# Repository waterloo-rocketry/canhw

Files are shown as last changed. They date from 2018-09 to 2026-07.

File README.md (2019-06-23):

## RocketCAN Hardware

This repository tracks the hardware development for the RocketCAN project. All schematics, board designs, and fabrication files are tracked in this repository. The corresponding software running on each board can be found in the `cansw_*` repositories. The CAN driver library used is tracked in the `canlib` repository.

All hardware files were developed in KiCAD.

### System Architecture

The RocketCAN project is an extension of the 2018 Flight Instrumentation project. The functions of the original Flight Instrumentation electronics are decoupled into several single-function modules connected by a Controller Area Network (CAN bus). The 2019 RocketCAN configuration consists of a radio board, an injector valve driver, a vent valve driver, a flight sensor suite, a system logger, and a GPS receiver. The modules freely share information over the CAN bus, allowing all modules to access resources such as the radio transceiver and sensor module. This minimizes the amount of component and functionality duplication, as well as power consumption (especially by the radio module). Power consumption is reduced further by allowing the radio board to control power to the rest of the system, forcing it into a low-power state while the rocket is idle. The resulting PCBs are also significantly smaller and easier to mount inside the rocket. Finally, RocketCAN’s configuration is easily extensible. A new subsystem simply needs to include a CAN communication module, after which it can communicate with all other boards on the bus. Potential extensions such as a flight computer, a state estimation module, or an air braking system would be able to use existing sensor data without implementing their own independent sensor suite.

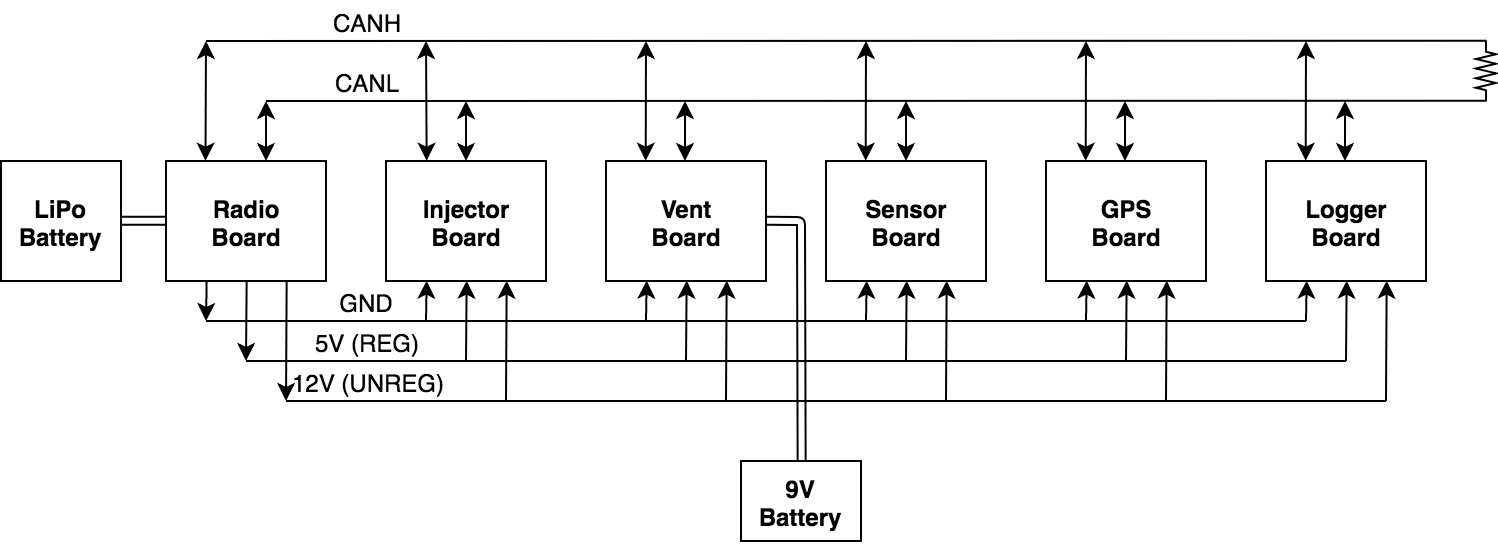
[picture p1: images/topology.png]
topo


At present, the radio board integrates with Waterloo Rocketry's Remote Launch Control System (RLCS), from which it receives instructions. It is also capable of broadcasting sensor data to RLCS.  The radio board communicates with the tower-side box of RLCS, which relays the data to the client-side box at mission control.

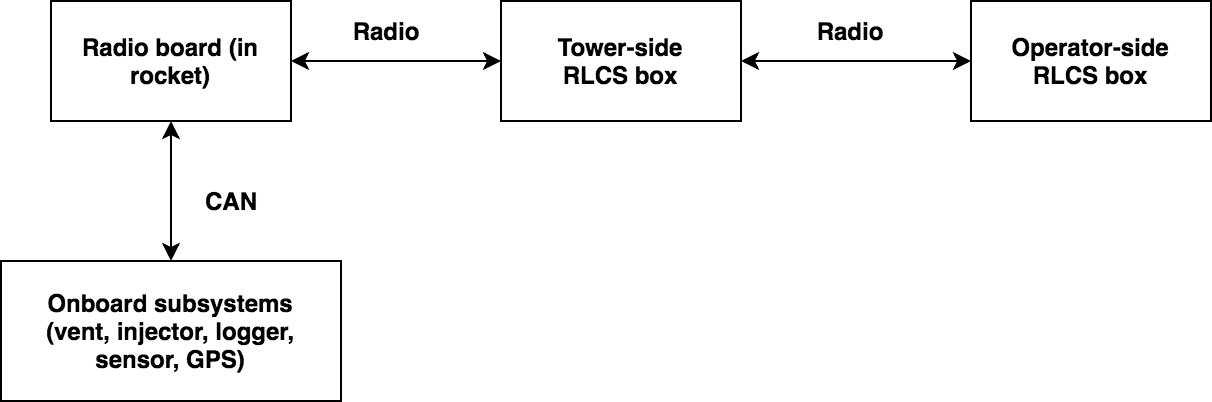
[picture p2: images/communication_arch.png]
comms


The CAN protocol was chosen for its high data rate, priority-based arbitration, and abundance of inexpensive hardware. The bus can safely be used by many boards at once without the risk of a low-priority message (eg. sensor data) preempting a high-priority message (eg. valve command). Microcontrollers with CAN modules, stand-alone CAN modules, and CAN transceivers are all widely available, making it cheap and simple to add CAN functionality to a subsystem.

Further descriptions and instructions for using each individual board are available in the README in the relevant board's directory.

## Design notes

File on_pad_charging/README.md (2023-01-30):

# On the Pad Charging
A charger board on the CAN bus that includes the battery, charging port connection, and additional power connections to live telemetry transmitter.
Clickup: https://app.clickup.com/8608989/v/li/176275976
Drive: https://drive.google.com/drive/folders/1WU_OsI1vf2b53sMAvz4AfjsN1jmYpsuN?usp=sharing

The system must provide CAN communication to the rocket from the ground side as long as the rocket is on the pad
The system should report the charge status, battery voltage, and current to CAN bus
The system should be able to turn off or on the CAN bus power. LTT should be kept 
The connector must be strong enough to stay in by itself, but weak enough to be pulled off by the rocket without affecting the launch

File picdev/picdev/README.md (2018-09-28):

This is a development board meant to be used for writing firmware for the CAN bus project while the main rocket boards are still in the hardware design phase. The board contains a PIC18F26K83 (which will be used on most subsystem boards inside the rocket) and a PIC16F1455 (which is used on the USB debug board). The PIC16F is connected to an external CAN module, allowing the two PICs to communicate with each other over CAN. 

The board is nicknamed "Keto" because it was borne out of a dislike of breadboards.

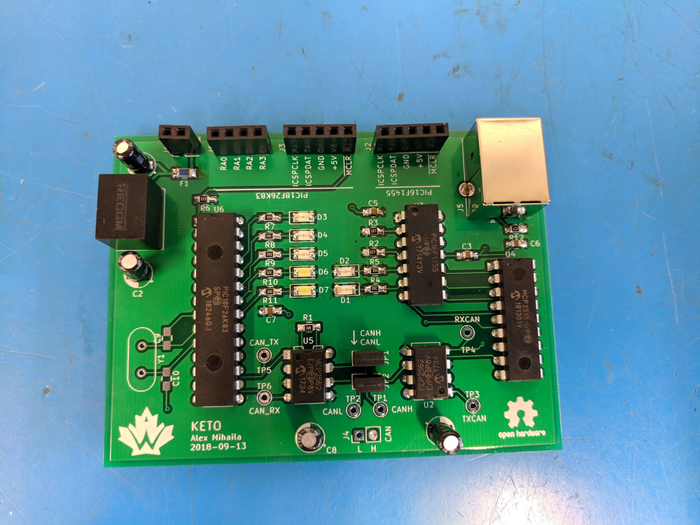
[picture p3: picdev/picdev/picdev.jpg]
picdev


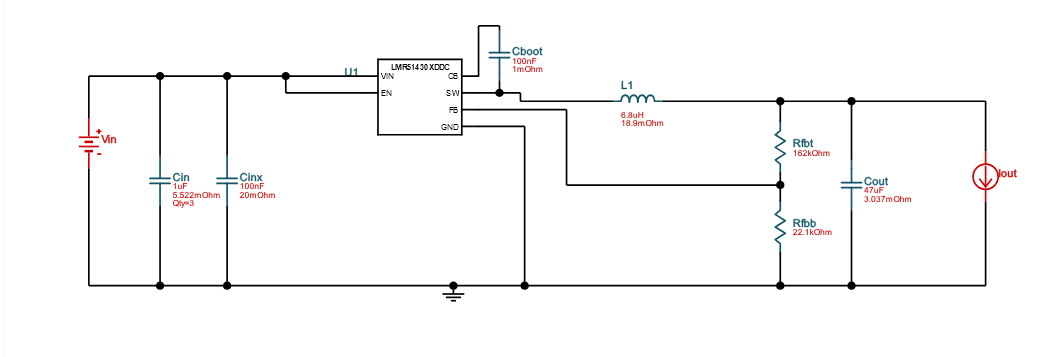
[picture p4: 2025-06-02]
rocket_power_board/WEBench Design.png

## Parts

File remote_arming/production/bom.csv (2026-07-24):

Designator | Footprint | Quantity | Value | LCSC Part #
BZ1 | Buzzer_12x9.5RM7.6 | 1 | CMI-1295-0585T
BZ2 | Buzzer_12x9.5RM7.6 | 1 | CMI-1295-1285T
C1, C2 | 0603 | 2 | 100nF
C10, C9 | 0603 | 2 | 26pF
C11 | 0603 | 1 | 0.39uF
C3 | 0603 | 1 | 10uF
C4 | 0603 | 1 | 0.1u
C5 | 0603 | 1 | 100n
C6 | 0603 | 1 | 0.33u
C7, C8 | 0603 | 2 | 0.1uF
D1, D2 | D_SOD-323_HandSoldering | 2 | CUS08F30
DB1, DR1, DW1 | 1206 | 3 | LED
F1 | 0603 | 1 | 0603L025YR
F2 | 1206 | 1 | Polyfuse 350mA
J1 | PinSocket_5x2.54_SMD_90deg_952-3198-1-ND | 1 | Conn_01x05_Female
J2 | BarrierBlock_ED2945-ND | 1 | Battery 1
J3 | connector_Harwin_G125-MH104M4-04AD000P | 1 | CAN connector
J4 | connector_Harwin_G125–MG10605M4P | 1 | Altimeter Input
J5 | JST_EH_S3B-EH_1x03_P2.50mm_Horizontal | 1 | SL Data Connector
J6 | connector_Harwin_G125–MG10605M4P | 1 | A1 Connections
JP1 | SolderJumper-2_P1.3mm_Open_RoundedPad1.0x1.5mm | 1 | M1 Pull Up
JP2 | SolderJumper-2_P1.3mm_Open_RoundedPad1.0x1.5mm | 1 | D1 Pull Up
Q1, Q2 | SOT-23_Handsoldering | 2 | BSS138
Q3 | SOT-23_Handsoldering | 1 | DMG2302UK
Q4 | TO-252-2 | 1 | AOD417
R1, R16, R18, R20, R21, R22, R5, R7, R9 | 0603 | 9 | 10K
R10 | 1206 | 1 | 4mR
R11 | 0603 | 1 | 200mR
R12 | 0603 | 1 | 2k
R13 | 0603 | 1 | 270R
R14 | 0603 | 1 | 5k
R15 | 0603 | 1 | 10kR
R17, R19, R6, R8 | 0603 | 4 | 27k
R2, R3, R4 | 0603 | 3 | 330R
TP1 | TestPoint_Pad_D2.0mm | 1 | SL_TX
TP2 | TestPoint_Pad_D2.0mm | 1 | CURR_CAN
TP3 | TestPoint_Pad_D2.0mm | 1 | CURR_BATT
U1 | SOIC-8_3.9x4.9mm_P1.27mm | 1 | MCP2562
U2 | SOIC-28W_7.5x18.7mm_P1.27mm | 1 | PIC18F26K83
U3 | Mag Switch | 1 | Mag Switch
U4 | SOT230P700X180-4N | 1 | UA78M05IDCYR
U5, U6 | SOT-23-5_HandSoldering | 2 | INA180
Y1 | Crystal_SMD_Abracon_ABM8G-4Pin_3.2x2.5mm | 1 | ABM8G-12.000MHZ-18-D2Y-T

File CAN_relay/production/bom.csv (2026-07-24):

Designator | Footprint | Quantity | Value | LCSC Part #
C1, C10, C11, C12, C13, C14, C16, C17, C18, C19, C21, C3, C8, C9 | 0603 | 14 | 100n
C2 | 0603 | 1 | 10n
C20, C23, C24 | 0805 | 3 | 22u
C22, C4 | 0603 | 2 | 1u
C5, C6 | 0603 | 2 | 2.2u
C7 | 0603 | 1 | 4.7u
D1 | 1206 | 1 | RED
D2 | 1206 | 1 | GREEN
D3, D4 | Nexperia_CFP3_SOD-123W | 2 | PMEG2010ER
D5, D6 | SOT-23 | 2 | ESDCAN01-2BLY | C1976606
F1 | 1206 | 1 | PTC 250mA
J2, J3 | connector_Harwin_G125-MH104M4-04AD000P | 2 | G125-MH104M4-04AD000P
R1, R2 | 0603 | 2 | 10k
R3, R4 | 0603 | 2 | 330R
R5, R6 | 0603 | 2 | 120R
U1 | LQFP-100_14x14mm_P0.5mm | 1 | STM32H750VBTx
U2, U3 | TCAN3413DDFR | 2 | TCAN3413DDFR
U4 | TPSM33606S3QRDNRQ1 | 1 | TPSM33606S3QRDNRQ1
X1 | Oscillator_SMD_Abracon_ASE-4Pin_3.2x2.5mm | 1 | ASE-4.000MHZ-L-C-T | C437121

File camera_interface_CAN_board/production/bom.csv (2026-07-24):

Designator | Footprint | Quantity | Value | LCSC Part #
C1, C2 | 0603 | 2 | 27pF
C10, C3, C4, C5, C9 | 0603 | 5 | 0.1uF
C11, C16, C6 | 0603 | 3 | 1uF
C12, C15 | 0603 | 2 | 2.2nF
C13, C14, C8 | 0805 | 3 | 10uF
C7 | 0603 | 1 | 10nF
D1 | 1206 | 1 | WHITE
D2 | 1206 | 1 | RED
D3 | 1206 | 1 | BLUE
D4 | D_SMF | 1 | SMF13CA
J1 | PinSocket_5x2.54_SMD_90deg_952-3198-1-ND | 1 | Programming Header
J2 | connector_Harwin_G125-MH104M4-04AD000P | 1 | G125-MH104M4-04AD000P
J3 | PinSocket_1x02_P1.27mm_Vertical | 1 | Analog_Video
J4 | connector_Harwin_G125–MG10605M4P | 1 | G125-MG10605M4P
R1, R2, R3, R8 | 0603 | 4 | 330R
R10 | 0603 | 1 | 120R
R11 | 0603 | 1 | 0R
R12, R14 | 0603 | 2 | 2k
R13 | 0603 | 1 | 1k
R4, R9 | 0603 | 2 | 10K
R5 | 0603 | 1 | 390k
R6 | 0603 | 1 | 3.3k
R7 | 0805 | 1 | 40mR
TP1 | TestPoint_Pad_D1.0mm | 1 | 5V
U1 | SOIC-28W_7.5x18.7mm_P1.27mm | 1 | canhw:PIC18F26K83
U2 | SOIC-8_3.9x4.9mm_P1.27mm | 1 | canhw:MCP2562
U3 | TPS25947xx | 1 | TPS259472ARPW
U4 | SOT-23-5_HandSoldering | 1 | INA180A3
U5 | SOP65P490X110-8N | 1 | TPS22958NDGKR
Y1 | Crystal_SMD_Abracon_ABM8G-4Pin_3.2x2.5mm | 1 | ABM8G-12.000MHZ-18-D2Y-T

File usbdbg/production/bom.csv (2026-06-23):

Designator | Footprint | Quantity | Value | LCSC Part #
C1, C2, C3 | 0603 | 3 | 0.1u
C15, C7 | 0603 | 2 | 10nF
C4 | 0603 | 1 | 10u
C6 | 0603 | 1 | 1uF
C8 | 0805 | 1 | 10uF
D1 | 1206 | 1 | GREEN
D2 | 1206 | 1 | RED
F1 | 1206 | 1 | 1A
J1 | PinSocket_5x2.54_SMD_90deg_952-3198-1-ND | 1 | Programming Header
J3 | CONN_SD-43045-001_04_MOL | 1 | BUS CONN
J4 | 2171790001_MOL | 1 | USB_C_Receptacle_USB2.0_14P
JP1, JP2 | PinHeader_1x02_P2.54mm_Vertical | 2 | Jumper
R1, R2 | 0603 | 2 | 330R
R3, R4 | 0603 | 2 | 10k
R5 | 0603 | 1 | 120R
R6, R7 | 0603 | 2 | 5.1k
R9 | 0603 | 1 | 6.65k
TP1, TP2, TP3, TP4 | KEYSTONE_5116 | 4 | TestPoint
U1 | SOIC-14_3.9x8.7mm_P1.27mm | 1 | PIC16F1455
U2 | SOIC-18W_7.5x11.6mm_P1.27mm | 1 | MCP2515
U3 | SOIC-8_3.9x4.9mm_P1.27mm | 1 | MCP2562
U4 | TPS25947xx | 1 | TPS259472ARPW
U5 | SOT-23-6 | 1 | USBLC6-2SC6

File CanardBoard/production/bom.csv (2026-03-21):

Designator | Footprint | Quantity | Value | LCSC Part #
C1, C10, C11, C14, C16, C18, C21, C22, C23, C24, C33, C34, C37, C40, C48, C50, C55, C57, C6, C60, C61, C62, C66, C67, C7, C73, C8, C81, C82, C83, C84, C9, C92, C93 | 0402 | 34 | 0.1uF | C85858
C12, C17, C47, C56, C63, C65, C74, C76, C89 | 0805 | 9 | 22uF | C86816
C13, C3, C5, C72, C91 | 0402 | 5 | 1uF | C77007
C15, C27, C28, C29, C30, C58, C59 | 0402 | 7 | 10nF | C91601
C19, C20, C25, C26, C51, C52, C53, C54, C70, C71, C85, C86, C87, C88 | 0603 | 14 | 0.1uF | C3011652
C2, C4, C49 | 0402 | 3 | 2.2uF | C77002
C31, C32, C90 | 0805 | 3 | 0.1uF | C882587
C35, C36, C38, C41, C43, C45, C68, C69, C79 | 1210 | 9 | 10uF | C77102
C39, C42, C44, C46 | A786MW227M1HLAV011 | 4 | 220uF | A786MW227M1HLAV011
C64 | 0402 | 1 | 220nF | C126524
C75 | 0402 | 1 | 33pF | C126506
C77, C78 | 1210 | 2 | 47uF | C77101
D1 | EAST1616RGBB2 | 1 | LED_RGBA | C6606484
D10, D17 | SOT-23 | 2 | ESDCAN01-2BLY | C1976606
D11, D12, D8, D9 | D_SMA | 4 | SMAJ28A | C148227
D13, D14, D15, D16, D4, D5, D6, D7 | D_SOD-523 | 8 | RB520S30T1G | C154821
D18, D19 | D_SMF | 2 | SMF15CA | C1851361
D2, D3 | D_SMA | 2 | SMAJ28CA | C148228
D20, D21, D22 | 0603 | 3 | RED | C2986060
F1, F2 | 1206 | 2 | 20A | C2838910
F3, F4, F5, F6 | 1206 | 4 | 10A | C41367232
F7, F8 | 1206 | 2 | 1.5A | C883133
F9 | 1206 | 1 | 5A | C41367229
FB1 | 0402 | 1 | BLM15AG121SN1D | C85812
J10 | connector_Harwin_G125-MH104M4-04AD000P | 1 | G125-MH104M4-04AD000P
J11 | Movella-1374028 | 1 | Movella-1374028
J12 | 1374027 | 1 | 1374027
J2 | microSD_HC_Molex_47219-2001 | 1 | Micro_SD_Card | C164170
J3, J4 | AMASS_XT30PW-M | 2 | XT30PW-M
J5 | G125MH10805M41AD1ADP | 1 | Motor 2
J6 | G125MH10805M41AD1ADP | 1 | Motor 1
J7 | G125MH10805M41AD1ADP | 1 | Motor 4
J8 | G125MH10805M41AD1ADP | 1 | Motor 3
J9 | USB_C_Receptacle_GCT_USB4105-xx-A_16P_TopMnt_Horizontal | 1 | USB_C_Receptacle_USB2.0_16P | C165948
L1 | SRP7050WA | 1 | 4.7uH | C19947706
Q1, Q2, Q3, Q4 | PowerPAK_SO-8_Single | 4 | SIR626DP-T1-RE3
Q10, Q7, Q8, Q9 | Infineon-PG-TSDSON-8 | 4 | 20N06D | C7543835
Q5, Q6 | 2N7002W | 2 | 2N7002W | C232391
R1, R14, R16, R2, R33, R34, R37, R38, R41, R42, R47, R48, R49, R8 | 0402 | 14 | 10k | C144807
R13, R15, R17, R19, R21, R23, R35, R36, R39, R40, R50, R52, R54, R55, R56, R59, R61, R67 | 0402 | 18 | 100k | C144809
R18, R20 | 0402 | 2 | 3.16k | C227034
R22, R24, R6, R7 | 0402 | 4 | 2.2k | C144773
R25, R26 | 0402 | 2 | 0R | C226739
R27, R28, R4, R5 | 0402 | 4 | 100R | C144808
R29, R30 | R_Shunt_Vishay_WSKW0612 | 2 | 1mR | C1517439
R3, R72, R73 | 0402 | 3 | 330R | C226996
R31, R32 | 0402 | 2 | 10R | C144805
R43, R44, R65 | 0805 | 3 | 120R | C727984
R45, R46 | 0402 | 2 | 5.1k | C144745
R51, R53, R68 | 0402 | 3 | 19.1k | C226835
R57 | 0402 | 1 | 34k | C227006
R58 | 0402 | 1 | 681R | C416567
R62 | 0402 | 1 | 43.2k | C278596
R63, R64, R69, R74, R75 | 0402 | 5 | 1k | C144789
R70, R71 | 0805 | 2 | 5m | C728267
R76 | 0805 | 1 | 1M | C228604
R9 | 1206 | 1 | 5.1k | C229719
U1 | LQFP-100_14x14mm_P0.5mm | 1 | STM32H733VGTx
U10, U11, U12, U9 | SOT-23-6 | 4 | LM74700
U13, U16, U6 | TCAN3413DDFR | 3 | TCAN3413DDFR
U14 | TPS25947xx | 1 | TPS259472 | C3662789
U15 | LGA-12_2x2mm_P0.5mm | 1 | LSM303AGR
U17 | LMR51460 | 1 | LMR51460 | C41802645
U18 | TPSM33606S3QRDNRQ1 | 1 | TPSM33610S3QRDNRQ1
U19, U20 | SOT-23-5 | 2 | INA180A3 | C122882
U2 | LGA-8_3x5mm_P1.25mm | 1 | MS5611-01BA
U21 | LSM6DSV32XTR | 1 | LSM6DSV32XTR
U22 | EMIF06MSD02N16 | 1 | EMIF06-MSD02N16 | C5267594
U23, U3 | WSON-6-1EP_2x2mm_P0.65mm_EP1x1.6mm | 2 | TVS3300DRV | C2863624
U4, U5 | LM749x0 | 2 | LM749x0
U7 | SOT-23-6 | 1 | USBLC6-2SC6 | C7519
U8 | MX25L25645GM2I-08G | 1 | MX25L25645GM2I-08G
X1 | Oscillator_SMD_Abracon_ASE-4Pin_3.2x2.5mm | 1 | ASE-4.000MHZ-L-C-T | C437121

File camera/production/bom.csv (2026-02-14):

Designator | Footprint | Quantity | Value | LCSC Part #
C1, C11, C12, C13, C14, C15, C16, C32, C33, C4, C7 | 0603 | 11 | 100n
C10 | 0603 | 1 | 4.7u
C17 | 0603 | 1 | 1u
C19, C20 | 0603 | 2 | 10p
C2 | 0603 | 1 | 22u
C21 | 0603 | 1 | 0.1u
C31 | 0603 | 1 | 10u
C49 | 0603 | 1 | 1uF | C49678
C5, C6 | 0603 | 2 | 33u
C50 | 0603 | 1 | 0.1uF | C49678
C8, C9 | 0603 | 2 | 2.2u
D1, D2, D5 | Nexperia_CFP3_SOD-123W | 3 | PMEG2010ER
D3 | 1206 | 1 | RED
D4 | 1206 | 1 | GREEN
F1 | 1206 | 1 | PTC 250mA
F2, F3 | 1206 | 2 | PTC 550mA
J2 | USB_Micro-B_Molex_47346-0001 | 1 | USB_B_Micro
J3 | PinHeader_2x07_P1.27mm_Vertical_SMD | 1 | Programmer
J5 | microSD_Molex_WM6698CT-ND | 1 | Micro_SD_Card
J6 | connector_Harwin_G125-MH104M4-04AD000P | 1 | G125-MH104M4-04AD000P
L1 | L_Bourns_SRP5030T | 1 | SRP5030T-3R3M
R1 | 0603 | 1 | 30mR
R10, R11, R12, R13, R14 | 0603 | 5 | 47k
R2 | 0603 | 1 | 40k
R3 | 0603 | 1 | 10k
R4 | 0603 | 1 | 33.2k 1%
R47, R48, R49 | 0603 | 3 | 10k | C17414
R5 | 0603 | 1 | 10k 1%
R8, R9 | 0603 | 2 | 100R
U1 | SOT-23-5_HandSoldering | 1 | INA180
U2 | SOT-23-6_Handsoldering | 1 | TPS562200
U4 | LQFP-100_14x14mm_P0.5mm | 1 | STM32H750VBTx
U5 | SOIC-8_3.9x4.9mm_P1.27mm | 1 | LTC2875-S8
U8 | SOIC-8_5.3x5.3mm_P1.27mm | 1 | MX25L25645GM2I-08G
Y1 | Crystal_SMD_Abracon_ABM8G-4Pin_3.2x2.5mm | 1 | ABM8G-32.000MHZ-B4Y-T

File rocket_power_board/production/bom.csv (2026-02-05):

Designator | Footprint | Quantity | Value | LCSC Part #
12IL, 5IL | TestPoint_Pad_1.0x1.0mm | 2 | TestPoint
C1, C13, C14, C15 | 0603 | 4 | 10uF
C10, C11, C23 | 0603 | 3 | 0.1u
C12, C19, C20, C22 | 0805 | 4 | 22uF
C16 | 0603 | 1 | 100nF
C17, C6 | 0603 | 2 | 2.2n
C18 | 0603 | 1 | 100p
C2 | 0603 | 1 | 0.1uF
C21, C8, C9 | 0603 | 3 | 1.0uF
C3, C4 | 0603 | 2 | 27pF
C5 | 0603 | 1 | 1uF
C7 | 0603 | 1 | 100pF
D1 | 1206 | 1 | RED
D2 | 1206 | 1 | BLUE
D3 | 1206 | 1 | WHITE
D4 | D_SOD-128 | 1 | PMEG3030EP
D5 | D_SOD-123F | 1 | SMF4L13CA
D6 | D_SOD-123F | 1 | SS24FL
D7 | D_SOD-123F | 1 | P4SMF5.0CA
D8 | D_SOD-123F | 1 | PMEG1020EH,115
F1 | 0154Series_LTF | 1 | 0154005.DRL
J1 | PinSocket_5x2.54_SMD_90deg_952-3198-1-ND | 1 | Programming Connector
J2 | connector_Harwin_G125-MH104M4-04AD000P | 1 | G125-MH104M4-04AD000P
J3 | TE_2-1437667-4 | 1 | 4DB-P108-02
L1 | IND_VLS6045EX-3R3N | 1 | 3.3uH
R1 | 0603 | 1 | 120R (DNP)
R10 | 0603 | 1 | 10mR
R11 | 0603 | 1 | 470k
R12 | 0603 | 1 | 14.7k
R13, R23, R25 | 0603 | 3 | 50k
R14, R29 | 0603 | 2 | 20k
R15, R28 | 0603 | 2 | 1.67k
R16, R19, R27, R30, R33, R4, R6 | 0603 | 7 | 10k
R17, R31 | 0603 | 2 | 71.5k
R18 | 0603 | 1 | 83.5k
R2 | 0603 | 1 | 220k
R20, R21, R34 | 0603 | 3 | 1.5k
R22 | 0603 | 1 | 400k
R24 | 0603 | 1 | 180k
R26 | 0603 | 1 | 56.2k
R3 | 0603 | 1 | 100k
R32 | 0603 | 1 | 30.5k
R5 | 0603 | 1 | 15k
R7 | 0603 | 1 | 500R
R8, R9 | 0603 | 2 | 330R
U1 | SOIC-8_3.9x4.9mm_P1.27mm | 1 | MCP2562
U2 | SOIC-28W_7.5x18.7mm_P1.27mm | 1 | PIC18F26K83-I/SO
U3, U7 | Texas_RPW0010A_VQFN-10_2x2mm | 2 | TPS259474ARPWR
U4 | SOT-23-5 | 1 | INA180A3
U5, U8 | SOT-23-5 | 2 | OPA333AIDR
U6 | SOT-23-6 | 1 | TPS563200
Y1 | Crystal_SMD_Abracon_ABM8G-4Pin_3.2x2.5mm | 1 | ABM8G-12.000MHZ-18-D2Y-T

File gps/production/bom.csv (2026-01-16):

Designator | Footprint | Quantity | Value | LCSC Part #
C1, C10, C13, C7, C9 | 0603 | 5 | 22pF
C11, C12 | 0805 | 2 | 26pF
C14, C2, C6 | 0603 | 3 | 0.1uF
C3 | 0603 | 1 | 10uF
C4, C5 | 0603 | 2 | 1uF
C8 | 0603 | 1 | 2.2uF
D1 | 1206 | 1 | WHITE
D2 | 1206 | 1 | RED
D3 | 1206 | 1 | BLUE
D4 | D_SOD-123F | 1 | KDZVTR3.6B
F1 | 0603 | 1 | 0ZCM0008FF2G
J1 | PinSocket_5x2.54_SMD_90deg_952-3198-1-ND | 1 | Programming Header
J2 | connector_Harwin_G125-MH104M4-04AD000P | 1 | G125-MH104M4-04AD000P
J3 | TAOGLAS_EMPCB.SMAFSTJ.B.HT | 1 | EMPCB.SMAFSTJ.B.HT
L1, L2 | 0603 | 2 | 47nH
R1 | 0603 | 1 | 100R
R2, R3, R4 | 0603 | 3 | 10k
R7, R8 | 0603 | 2 | 160
R9 | 0603 | 1 | 200mR
TP1 | TestPoint_THTPad_1.0x1.0mm_Drill0.5mm | 1 | RX
TP2 | TestPoint_THTPad_1.0x1.0mm_Drill0.5mm | 1 | TX
TP3, TP4 | TestPoint_Keystone_5000-5004_Miniature | 2 | 36-5001-ND
U1 | QFN16_M10578_ANT | 1 | M10578-A2
U2 | SOIC-28W_7.5x18.7mm_P1.27mm | 1 | PIC18F26K83
U3 | SOIC-8_3.9x4.9mm_P1.27mm | 1 | MCP2562
U4 | SOT-23-5_HandSoldering | 1 | SPX3819M5-L-3-3
U5 | SOT-23-5_HandSoldering | 1 | INA180
Y1 | Crystal_SMD_Abracon_ABM8G-4Pin_3.2x2.5mm | 1 | ABM8G-12.000MHZ-18-D2Y-T

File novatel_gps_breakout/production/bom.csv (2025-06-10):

Designator | Footprint | Quantity | Value | LCSC Part #
C1, C2 | 0805 | 2 | 10u
F1 | 1206 | 1 | 350m
J1 | PTF11001LD | 1 | PTF-110-01-L-D
J2 | connector_Harwin_G125–MG10605M4P | 1 | Harwin Gecko
J3 | AMPHENOL_GMSB0522132EU | 1 | GMSB0522132EU
U1 | SOT-23-5_HandSoldering | 1 | TLV75533PDBV

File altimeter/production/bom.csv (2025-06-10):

Designator | Footprint | Quantity | Value | LCSC Part #
BZ1 | CUI_CMI-9605-1280T | 1 | CMI-9605-1280T
C1, C27, C28, C5 | 0805 | 4 | 10uF
C10, C11, C12, C17, C18, C20, C29, C7, C8 | 0805 | 9 | 100nF
C13, C9 | 0805 | 2 | 2.2uF
C14, C48 | 0805 | 2 | 4.7uF
C15, C16, C3, C30, C31, C49 | 0805 | 6 | 1uF
C19, C2, C35, C38, C42, C50 | 0805 | 6 | 0.1uF
C21, C22, C23, C24, C36, C37, C39, C40, C41, C43 | 0805 | 10 | 47nF
C25 | 0805 | 1 | 0.33uF
C26 | 0805 | 1 | 0.22uF
C32, C33, C34 | 0805 | 3 | 22uF
D2 | 1206 | 1 | YELLOW
D3 | 1206 | 1 | RED
D4 | 1206 | 1 | GREEN
D5 | Nexperia_CFP3_SOD-123W | 1 | PMEG2010ER,115
F1 | 2920 | 1 | 2920L700/24SLER
FB1 | 0805 | 1 | BLM21PG221SN1D
J1 | connector_Harwin_G125–MG10605M4P | 1 | GPS
J2 | connector_Harwin_G125–MG10605M4P | 1 | RocketCAN
J3 | connector_Harwin_M80-5000642 | 1 | M80-5000642
J4 | TE_2-1437667-4 | 1 | 4DB-P108-02
J5 | PololuAltIMUv6 | 1 | Pololu
J6 | PinSocket_2x02_P1.27mm_Vertical_SMD | 1 | Programmer
J7 | microSD_Molex_WM6698CT-ND | 1 | Micro_SD_Card
L1 | IND_IHLP-2525CZ_VIS | 1 | IHLP2525CZER2R2M11
R1 | 0805 | 1 | 0.05R
R10, R25, R32, R38, R39, R46, R52, R7, R8, R9 | 0805 | 10 | 5k
R11, R13, R29, R43 | 0805 | 4 | 60k
R12, R14, R28, R31, R35, R42, R45, R49 | 0805 | 8 | 20k
R15 | 0805 | 1 | 0.002R
R16, R75 | 0805 | 2 | 0.015R
R17, R18, R19, R20, R3, R4, R76, R77 | 0805 | 8 | 10R
R21 | 0805 | 1 | 33.2k
R22, R23, R24, R26, R37, R40, R51 | 0805 | 7 | 10k
R27, R36, R41, R50 | 0805 | 4 | 175R
R30, R44 | RES_PWR263S_BRN | 2 | PWR263S-35-5R00F
R33, R47 | 0805 | 2 | 1.5k
R34, R48 | 0805 | 2 | 500R
R67, R68, R69, R70, R71 | 0805 | 5 | 10kR
R72, R73, R74 | 0805 | 3 | 100R
U1 | SOIC-8_3.9x4.9mm_P1.27mm | 1 | MCP2562
U10, U12, U13, U9 | TLP3543A__6P4X7P12_TOS | 4 | TLP3543A(TP1,F)
U11, U14 | SOT-363_SC-70-6_Handsoldering | 2 | INA210AIDCKT
U18 | SOT-23-5_HandSoldering | 1 | INA180A3
U2 | SOT-23-5 | 1 | INA180A3
U4 | LQFP-100_14x14mm_P0.5mm | 1 | STM32H750VBTx
U5 | Mag Switch | 1 | Mag Switch
U6 | SOT-223 | 1 | NCV33275ST5.0T3G
U7 | SOT-23-6 | 1 | TPS563200DDCR
U8 | VSSOP-8_3x3mm_P0.65mm | 1 | INA2180A4IDGKR

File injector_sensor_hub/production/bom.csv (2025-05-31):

Designator | Footprint | Quantity | Value | LCSC Part #
2A1, 2A2, 2A3, 2A4, 2A5, 3A1, 3A2, 3A3 | TestPoint_Keystone_5005-5009_Compact | 8 | TestPoint
C1 | 0805 | 1 | 10uF
C2, C3 | 0805 | 2 | 0.1uF
C4 | 0805 | 1 | 0.1 uF
C5, C6 | 0805 | 2 | 27pF
D1 | 1206 | 1 | BLUE
D2 | 1206 | 1 | WHITE
D3 | 1206 | 1 | RED
F1, F2 | 1206 | 2 | 350mA
H1, H2 | MountingHole_3.2mm_M3_Pad | 2 | +5V
H3, H4 | MountingHole_3.2mm_M3_Pad | 2 | MountingHole_Pad
J1 | connector_Harwin_G125–MG10605M4P | 1 | CAN_Connector
J10, J3, J4, J6, J8 | JST_PH_S2B-PH-K_1x02_P2.00mm_Horizontal | 5 | Conn_01x02_Female-Connector
J2 | PinSocket_5x2.54_SMD_90deg_952-3198-1-ND | 1 | Programming Header
J5, J7, J9 | JST_PH_S3B-PH-K_1x03_P2.00mm_Horizontal | 3 | Conn_01x03_Female
R1, R10, R11, R12, R13, R14, R15, R16, R17, R18, R19, R2, R20, R21, R22, R9 | 0805 | 16 | TBD
R3 | 0805 | 1 | 10K
R4 | 0805 | 1 | 180R
R5 | 0805 | 1 | 220R
R6, R7 | 1206 | 2 | 130mR
R8 | 0805 | 1 | 300R
TP1 | TestPoint_Keystone_5005-5009_Compact | 1 | TP_5V
TP4 | TestPoint_Keystone_5005-5009_Compact | 1 | TP_12V
U1 | SOIC-8_3.9x4.9mm_P1.27mm | 1 | MCP2562
U2 | SOIC-28W_7.5x17.9mm_P1.27mm | 1 | PIC18F26K83
U3, U4 | SOT-23-5_HandSoldering | 2 | INA180
Y1 | Crystal_HC49-4H_Vertical | 1 | Crystal

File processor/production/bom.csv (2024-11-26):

Designator | Footprint | Quantity | Value | LCSC Part #
C1 | 0805 | 1 | 10uF | C15850
C10, C22, C3 | 0805 | 3 | 4.7uF | C1779
C11, C13, C15, C2, C20, C21, C5, C6, C7, C8, C9 | 0805 | 11 | 0.1uF | C49678
C12, C14, C16 | 0805 | 3 | 1uF | C28323
C17 | 0805 | 1 | 0.01uF | C1710
C18, C19 | 0805 | 2 | 2.2uF | C377773
C4 | 0805 | 1 | 22uF | C45783
D1 | 1206 | 1 | LED_R | C7496845
D2 | 1206 | 1 | LED_G | C7496843
D3 | 1206 | 1 | LED_B | C434440
D4 | 1206 | 1 | PWR | C434434
F1 | 1206 | 1 | Polyfuse 1A | C20800
FB1 | 0603 | 1 | PE-0603PFB121ST | C139186
JP3 | SolderJumper-3_P1.3mm_Open_Pad1.0x1.5mm_NumberLabels | 1 | BOOT_CTL
L1 | IND_DFE252012PD-1R0M=P2_MUR | 1 | 1uH | C2917900
R1 | 1206 | 1 | 33 mR | C912764
R10, R11, R12, R13, R14, R15, R16, R17, R18, R19, R20, R21, R7, R9 | 0805 | 14 | 10kΩ | C17414
R2 | 0805 | 1 | 453kΩ | C101739
R3 | 0805 | 1 | 100kΩ | C149504
R4, R8 | 0805 | 2 | 150Ω | C17471
R5, R6 | 0805 | 2 | 330Ω | C17630
U1 | SOIC-8_3.9x4.9mm_P1.27mm | 1 | MCP2562 | C191417
U2 | SOT-23-5_HandSoldering | 1 | INA180 | C2059240
U3 | DRL0006A | 1 | TLV62568ADRLR | C398372
U4 | LQFP-100_14x14mm_P0.5mm | 1 | STM32H733VGTx | C730160
U5 | LGA-14L_2p5X3p0X0p86_STM | 1 | LSM6DSV32X | C22461202
X1 | Oscillator_SMD_Abracon_ASE-4Pin_3.2x2.5mm | 1 | ASE-4.000MHZ-L-C-T | C437121

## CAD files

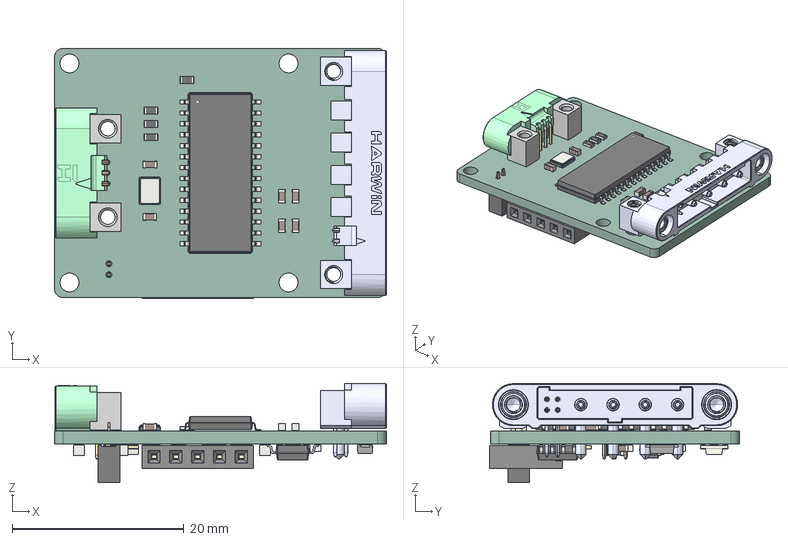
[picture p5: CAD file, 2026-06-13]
camera_interface_CAN_board/output/camera_board.step
38.7 x 29.1 x 11.6 mm
G125-3270696
G125-1060005_BENT x 3
G125-1070005_BENT x 3
R_0603_1608Metric x 8
C_0603_1608Metric x 13
SOIC-28W_7.5x18.7mm_P1.27mm
Crystal_SMD_Abracon_ABM8G-4Pin_3.2x2.5mm
g125-mh104m4-04ad000p
LED_1206_3216Metric x 3
C_0805_2012Metric x 3
SOIC-8_3.9x4.9mm_P1.27mm
D_SMF
M20-7910542R
MOLD
BODY_MUA08A
LEAD_MUA08A x 8
PinSocket_1x02_P1.27mm_Vertical
R_0805_2012Metric
SOT-23-5
camera_interface_CAN_board_PCB

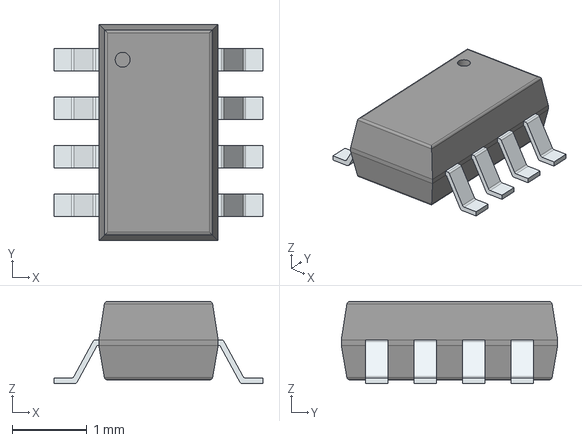
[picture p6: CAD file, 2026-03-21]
CAN_relay/3D_Models/TCAN3413DDFR.stp
2.80 x 2.90 x 1.10 mm
PinsArrayLR

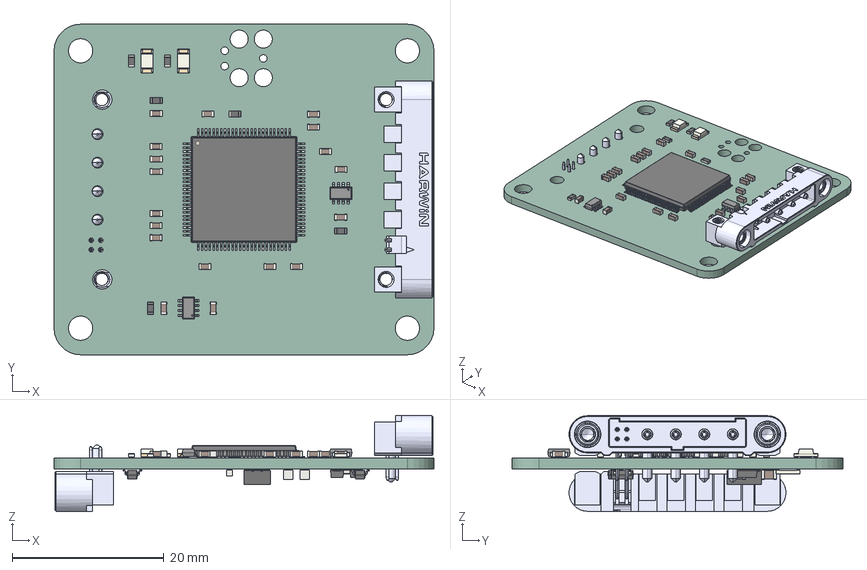
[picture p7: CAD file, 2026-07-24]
CAN_relay/CAN_relay.step
50.0 x 43.5 x 12.6 mm
g125-mh104m4-04ad000p x 2
C_0603_1608Metric x 20
R_0603_1608Metric x 6
PinsArrayLR x 2
LED_1206_3216Metric x 2
LQFP-100_14x14mm_P0.5mm
SOT-23 x 2
MOLD_CPOMPOUND_AF0
SOLID1-489_AF0
SOLID1-490_AF0
SOLID1-491_AF0
SOLID1-492_AF0
SOLID1-493_AF0
SOLID1-494_AF0
SOLID1-495_AF0
SOLID1-496_AF0
SOLID1-497_AF0
SOLID1-498_AF0
C_0805_2012Metric x 3
6081697a-9268-11ed-8af4-a0cec80452fd_part x 2
60816e3e-9268-11ed-8af4-a0cec80452fd_part x 2
6081710e-9268-11ed-8af4-a0cec80452fd_part x 2
6081737a-9268-11ed-8af4-a0cec80452fd_part x 2
Fuse_1206_3216Metric
CAN_relay_PCB

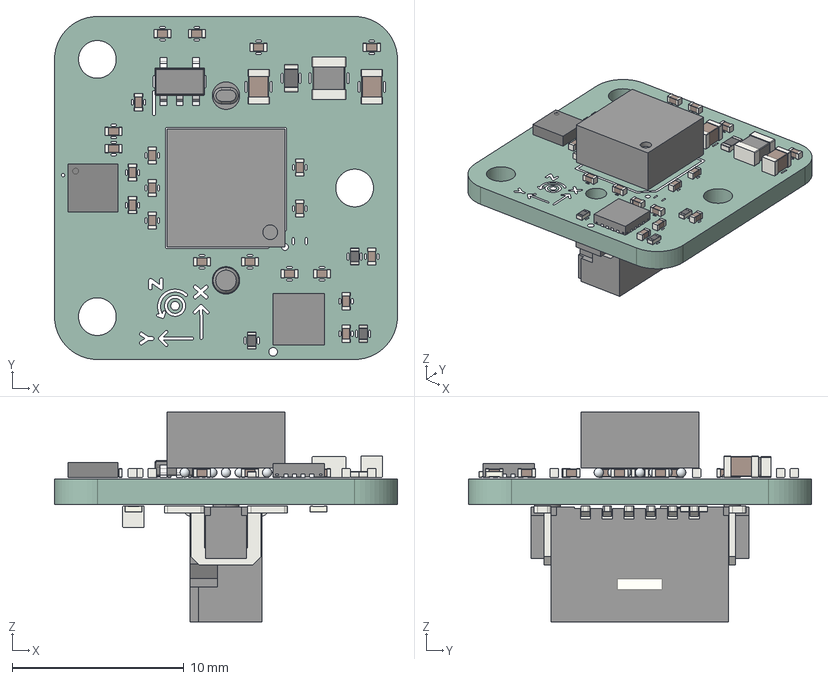
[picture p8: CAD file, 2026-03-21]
CanardBoard/AD_Breakout_Board/Output/AD_Breakout_REVA.step
20.0 x 20.0 x 12.2 mm
C_0402_1005Metric x 21
R_0402_1005Metric x 7
L_1008_2520Metric
ADXL380-1BCCZ-RL7
C_0805_2012Metric x 3
A2
A3
A4
A5
A6
B1
B3
B4
B5
B7
C1
C2
C6
C7
D1
D2
D6
D7
E1
E2
E6
E7
F1
F3
F4
F5
F7
G2
G3
G4
G5
G6
BODY-SOT
LEAD-SOT x 5
R_0603_1608Metric
LP_FR_1_27_MV_1_75_CONTACT.3 x 12
GEH_FR_1_27_12_MV_1_75_HOUSING
LR_FR_1_27_BOARD_LOCK.1 x 2
AD_Breakout_silkscreen x 2
AD_Breakout_PCB

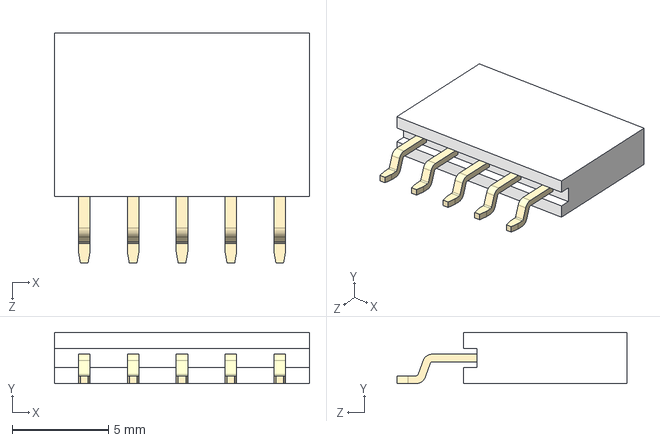
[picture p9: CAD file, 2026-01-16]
gps/Symbol_Footprt/BG300_05_A_L_A/BG300-05-X-X-A_REVC.step
13.2 x 2.65 x 12.0 mm
body^BG301-xxx
pin^BG301-xxx x 5

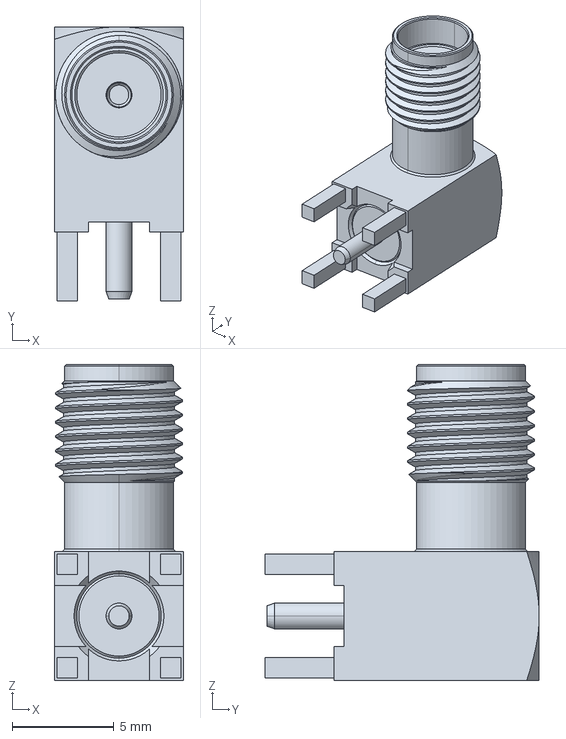
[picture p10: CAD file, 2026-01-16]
gps/Symbol_Footprt/SMA_Conn/c-3-1478978-1-f-3d.stp
6.35 x 13.5 x 15.6 mm

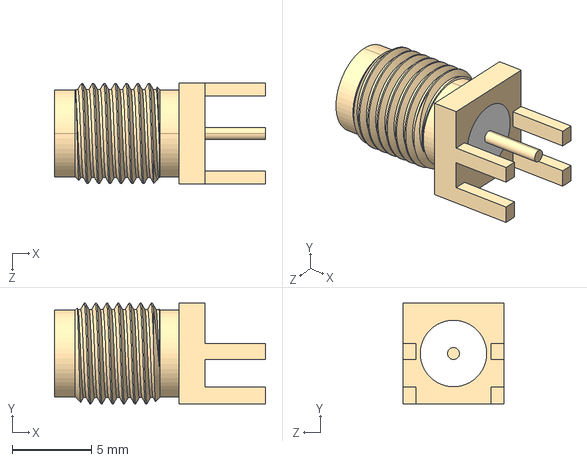
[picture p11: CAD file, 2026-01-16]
gps/Symbol_Footprt/SMA_Edge/CON-SMA-EDGE-S.step
13.3 x 6.35 x 6.35 mm

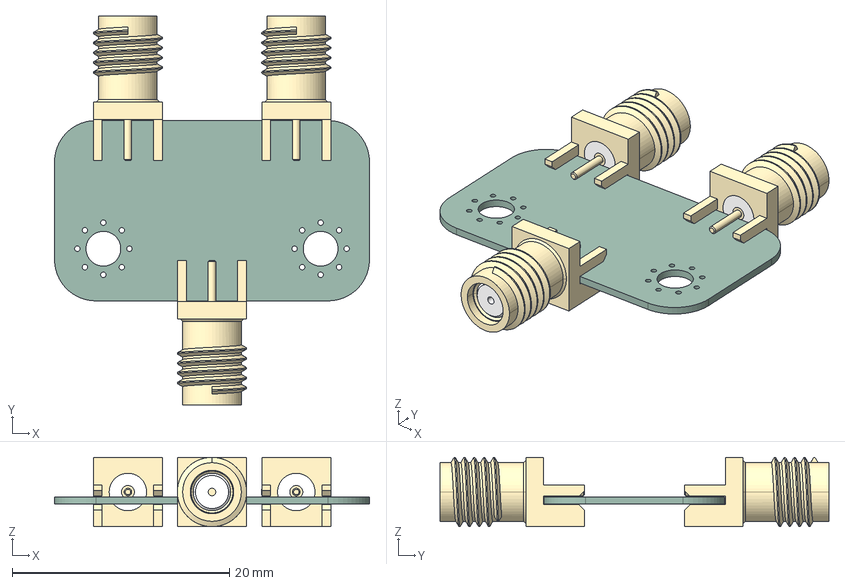
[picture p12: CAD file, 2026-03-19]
live_telemetry/power-splitter/power-splitter.step
29.0 x 35.8 x 6.38 mm
EMPCB.SMAFSTJ.B.HT x 3
power-splitter_PCB

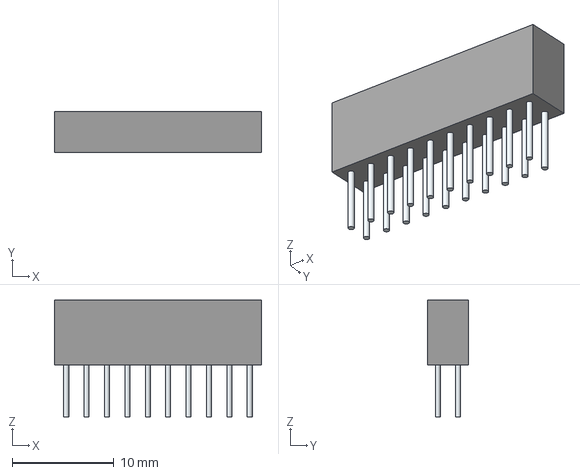
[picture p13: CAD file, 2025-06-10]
novatel_gps_breakout/3d/PTF-110-01-L-D.stp
20.3 x 4.00 x 11.4 mm
Leads x 20

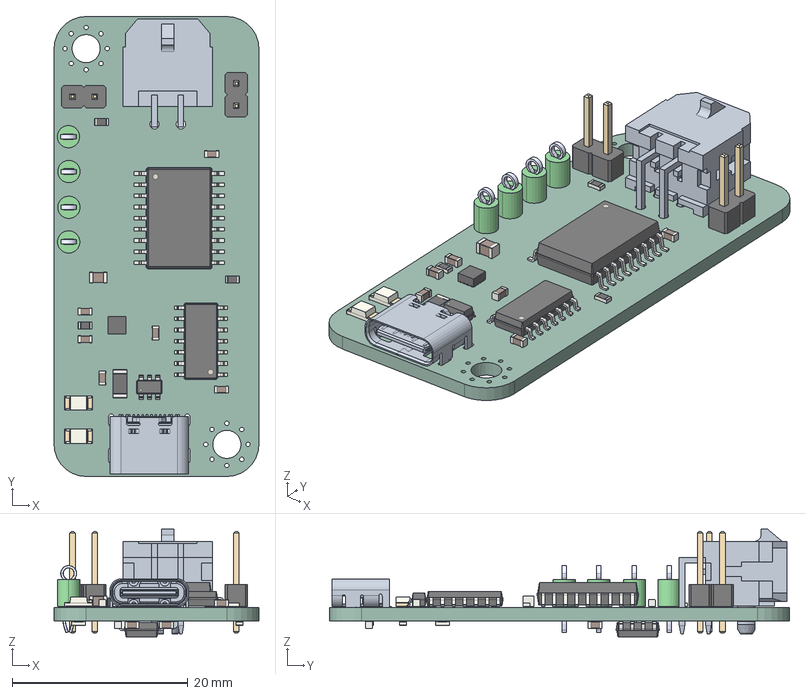
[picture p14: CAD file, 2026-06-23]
usbdbg/usbdbg.step
23.3 x 52.3 x 12.3 mm
C_0603_1608Metric x 9
PinHeader_1x02_P254mm_Vertical x 2
R_0603_1608Metric x 6
SOIC-18W_7.5x11.6mm_P1.27mm
SOIC-14_3.9x8.7mm_P1.27mm
C_0805_2012Metric
LED_1206_3216Metric x 2
SOT-23-6
MOLD
Fuse_1206_3216Metric
SOIC-8_3.9x4.9mm_P1.27mm
usbdbg_PCB

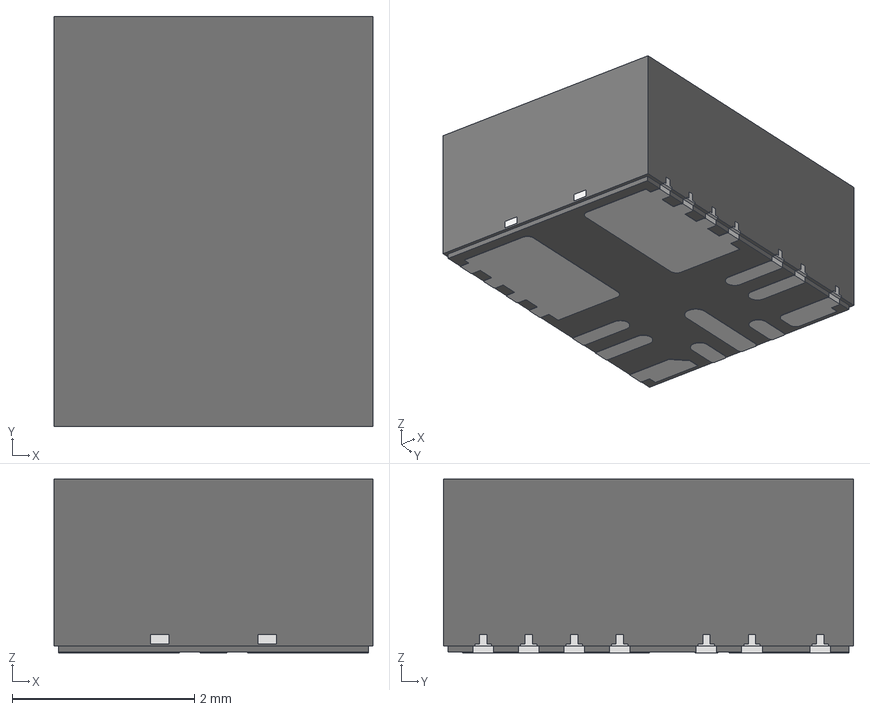
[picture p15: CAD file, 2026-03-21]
CAN_relay/3D_Models/RDN0011B.stp
3.50 x 4.50 x 1.91 mm
MOLD_CPOMPOUND_AF0
SOLID1-489_AF0
SOLID1-490_AF0
SOLID1-491_AF0
SOLID1-492_AF0
SOLID1-493_AF0
SOLID1-494_AF0
SOLID1-495_AF0
SOLID1-496_AF0
SOLID1-497_AF0
SOLID1-498_AF0

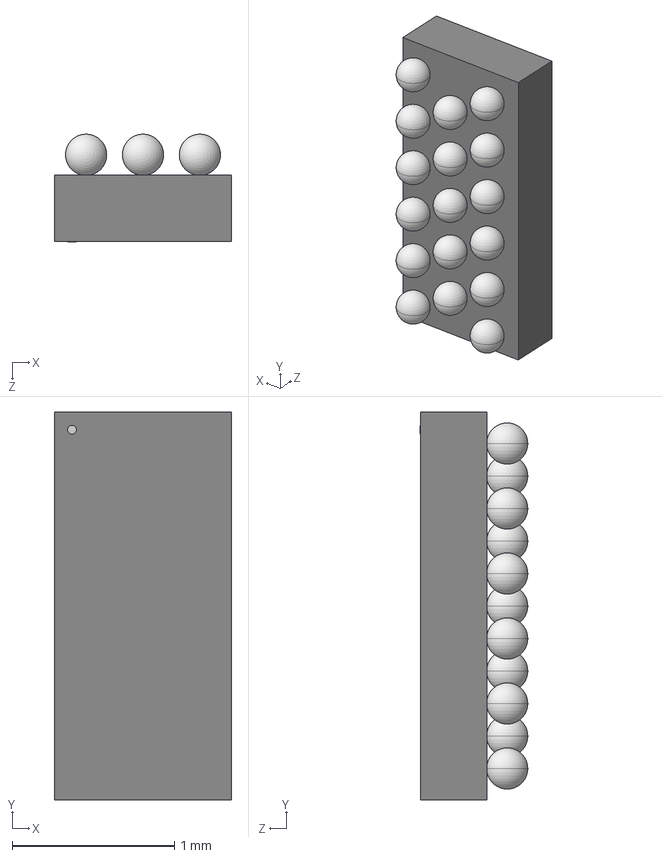
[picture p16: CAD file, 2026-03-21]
CanardBoard/3D_Models/EMIF06-HSD03F3.stp
1.09 x 2.39 x 0.663 mm

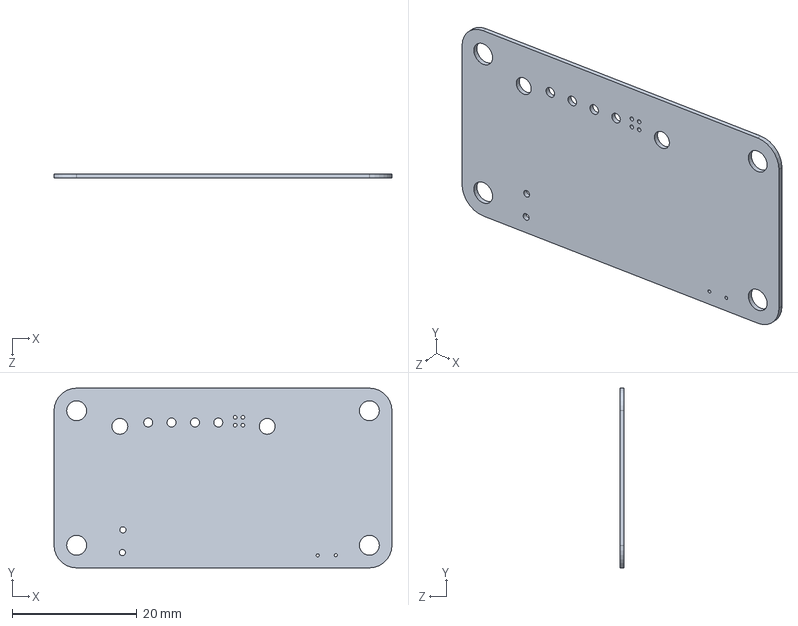
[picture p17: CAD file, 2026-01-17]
gps/gps_2_PCB.step.SLDPRT
54.3 x 28.9 x 0.665 mm

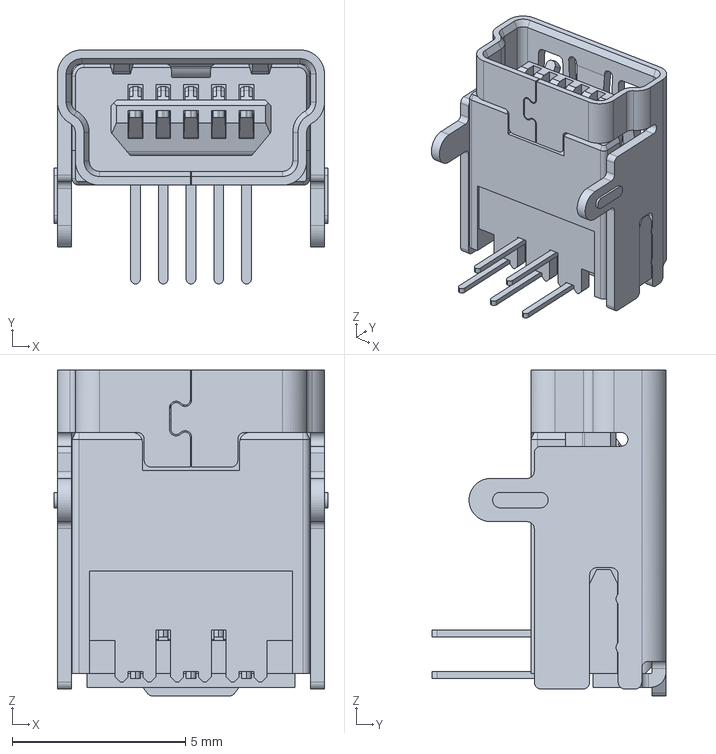
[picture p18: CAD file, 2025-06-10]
novatel_gps_breakout/3d/GMSB0522132EU.step
7.90 x 6.75 x 9.40 mm

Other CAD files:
gps/gps_2.step.SLDASM
CanardBoard/3D_Models/SIR626DP-T1-RE3.STEP
gps/SOIC-28W_7.5x18.7mm_P1.27mm.step.SLDPRT
CanardBoard/3D_Models/REF2041AIDDCR.stp
CanardBoard/3D_Models/1373827.stp
CanardBoard/3D_Models/2N7002W.stp
CanardBoard/3D_Models/472192001.stp
CanardBoard/3D_Models/A786MW227M1HLAV011.stp
CanardBoard/3D_Models/ADS1219IRTER.stp
CanardBoard/3D_Models/ADXL380-1BCCZ-RL7.stp
CanardBoard/3D_Models/ADXRS649BBGZ.stp
CanardBoard/3D_Models/BSZ024N04LS6ATMA1.stp
CanardBoard/3D_Models/EAST1616RGBB2.stp
CanardBoard/3D_Models/EMIF06-MSD02N16.stp
CanardBoard/3D_Models/G125-MH10805M4-1AD1ADP.stp
CanardBoard/3D_Models/LGA-14L_2p5X3p0X0p86_STM.step
CanardBoard/3D_Models/LM74910QRGERQ1.stp
CanardBoard/3D_Models/LMR51450FNDRRR.stp
CanardBoard/3D_Models/MX25L25645GM2I-08G-TR.stp
CanardBoard/3D_Models/PTVS30VZ1UPAZ.stp
CanardBoard/3D_Models/SRP7050WA.stp
CanardBoard/3D_Models/TPS25210LRPWR.stp
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

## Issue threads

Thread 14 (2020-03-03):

Boards list 26pF for oscillator filter caps, but these are not readily available.

zx100x100, 2020-03-03:
We already use 27pF as a substitution, we should fix the schematics to address this.

amihaila, 2020-03-03:
fixed in `537802ed4601e1b5135b2eaccdbe543847dbf9fd`

Closed 2020-03-03.

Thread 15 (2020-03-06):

Add Battery number to silkscreen on Remote Arming

zx100x100, 2020-03-06:

zx100x100, 2020-03-12:
add battery numbers to silk screen
fix can connector pinout to mach other boards
 put diodes and voltage sensing down stream of mag switches for easier power-up confirmation

zx100x100, 2020-03-21:
OUT and IN pins are backwards for mag switches

zx100x100, 2020-05-24:
Switch to 90 degree JST for altitude connector to avoid pinching wires with airframe

zx100x100, 2020-09-25:
label jumpers

zx100x100, 2020-11-18:
all this was dealt with in V2

Closed 2020-11-18.

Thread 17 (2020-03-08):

Not all schematic PDFs are up to date.

zx100x100, 2020-03-08:

amihaila, 2020-03-08:
fixed in `ac6cfa6a2df630c2c32a38dd9e6480b5804a335e`

Closed 2020-03-08.

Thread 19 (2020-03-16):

resistor value of R4 and R3 on logger should be 160, not 330

zx100x100, 2020-03-16:

zx100x100, 2020-03-16:
Package of U3 is wrong

zx100x100, 2020-03-16:
or part number - used MIC5504-3.3YM5-TR

Closed 2022-01-16.

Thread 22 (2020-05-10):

RF footprint needs to be improved

JaredWatson, 2020-05-10:
Currently the RF footprint used on the GPS board and the Live Telemetry board had extremely small pads that make soldering it a pain in the butt. In the future the amount of soldering space should probably be expanded (but not enough to shrink the space of the RF trace, it's already smaller than 120 mils and we don't want to lose that sweet sweet RF integrity).

QuantumManiac, 2020-05-11:
I did a bit of testing, and it seems like it's pretty simple to have different sized pads on different layers.

In the _Pad Properties_ window, there's a Copper setting which allows you to change the layers that the copper and other layers are on for the pad:
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

My solution is to overlap two pads at each through-hole, with one pad having F.Cu and F.Mask and the other B.Cu and B.Mask

Here's a view of a modified SMA connector in the footprint editor modified using the above method:
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
Notice that while the front pads are 2.2 mm, the back ones are much larger, at 3 mm

3D Views - front and back comparison:
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

If I got some measurements for what the pads should be on each side, I would be happy to modify the footprint.

JaredWatson, 2020-05-12:
Looks good, I'll leave a more formal review on the actual PR. This is definitely the footprint people should be using for SMA stuff in the future.

Closed 2020-05-21.

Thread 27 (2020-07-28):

Issues with first version of Live Telemery boards

dwkletke, 2020-07-28:
Issues marked with LTT are for the Live Telemetry Transmitter and issues marked with LTR are for the Live Telemetry Receiver.

dwkletke, 2020-07-28:
LTT: R12 and R13 silk screen labels need to be moved to become completely visible.

dwkletke, 2020-07-28:
LTT: Add values for R10, R11, and R_sense to schematic.

dwkletke, 2020-07-28:
LTT: Fix C5 and C9 labelling for +/- (right now is backwards).

dwkletke, 2020-07-28:
LTT: Add labeling for +/- on battery screw terminal.

dwkletke, 2020-07-28:
LTR: Add mounting hole(s).

dwkletke, 2020-07-28:
LTT and LTR: Add arrowhead to silk screen for MCLR pin on programming header.

Closed 2023-07-09.

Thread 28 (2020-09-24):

Vent board V2 Issues

zx100x100, 2020-09-24:
MCLR silkscreen reads 3.3V, but MCLR is actually a 5V line on this board

zx100x100, 2020-12-24:
A jumper was never added to allow vent to draw from the CAN bus. in addition, I'm not sure why we ever Ok'd a JST for flight critical connections

zx100x100, 2021-05-16:
Forgot to close this when we merged the V2.1 PR

Closed 2021-05-16.

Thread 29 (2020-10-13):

GPS board led label

Rio6, 2020-10-13:
The led connected to fix signal is labeled as "white", better label it as "fix" so it's more clear.

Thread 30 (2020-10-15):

Mini sensor issues

zx100x100, 2020-10-15:
1. The PTC fuse values should be labelled

2. this board could really do with some SMD test points.

zx100x100, 2020-12-17:
MCLR silkscreen does not indicate MCLR voltage

rdakhil, 2023-04-05:
some ground test points would be nice to have in the next respin

also standoffs are there in the CAD but they are very thin. the plating should be changed to be about as thick as the mounting holes

JasonBrave, 2023-05-23:
Clock source(oscillator) is not isolated, result interference from CAN, cause PIC think external oscillator failure.

BluCodeGH, 2023-07-09:
Recent comments are not addressed.

Joe-Joe-Joe-Joe, 2023-07-09:
Has this board not been respun since this issue was raised?

Closed 2023-07-09.

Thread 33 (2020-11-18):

Remote Arming Issues

zx100x100, 2020-11-18:
Arming currently has a 1.7V dropout regulator, that is way to high
replace with https://www.digikey.com/en/products/detail/texas-instruments/LM2931AMX-5-0-NOPB/334920

zx100x100, 2021-05-14:
Make the mag switch mounting holes make sense

Closed 2023-07-09.

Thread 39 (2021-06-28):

Logger CAN connector pinout is wrong

BluCodeGH, 2021-06-28:

Closed 2022-01-16.

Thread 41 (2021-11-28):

PICam CAN connector pinout is wrong

BluCodeGH, 2021-11-28:

Closed 2023-07-09.

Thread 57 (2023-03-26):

Charging Board Issues

BluCodeGH, 2023-03-26:
- There is no current sensing on VCC out of the powerpath switcher, which means that when we are powering the rocket off of the battery we have no idea what the current draw on the 12V line from the CAN bus is.
- There is significant interference between the 24->13V regulator (likely the inductor?) and its current sensing voltage. The current sense voltage at idle is about 12 mV and we're seeing 500 mV spikes on the pin highly regularly at 8.2 kHz.

Closed 2023-06-03.

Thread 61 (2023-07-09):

Minisensor rev. 2 issues

Joe-Joe-Joe-Joe, 2023-07-09:
New respin problems:

              missing solder standoffs,
              doesn't match the required design from Rocket CAD, make the two agree

_Originally posted by @zx100x100 in https://github.com/waterloo-rocketry/canhw/issues/30#issuecomment-1494538198_

              some ground test points would be nice to have in the next respin

              also standoffs are there in the CAD but they are very thin. the plating should be changed to be about as thick as the mounting holes

_Originally posted by @rdakhil in https://github.com/waterloo-rocketry/canhw/issues/30#issuecomment-1496845932_

              Clock source(oscillator) is not isolated, result interference from CAN, cause PIC think external oscillator failure.

_Originally posted by @JasonBrave in https://github.com/waterloo-rocketry/canhw/issues/30#issuecomment-1558394349_

Joe-Joe-Joe-Joe, 2024-03-28:
Closed by retiring minisensor lol

Closed 2024-03-28.

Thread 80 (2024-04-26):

Charging Board Re-respin todo

AshTheEngiqueer, 2024-04-26:
C27 can be an 0805 to match C26 and C28
R17 and R23 can be an 0805 to match R39
The layout could be nicer (like fix some of the scuffed traces, and have components align better in general)

AshTheEngiqueer, 2024-06-22:
13V current sense is scuffed, voltage sense is gigafucked - smth to do with inductor? unclear.

Lucifersan, 2024-06-29:
indicate that the motor control harwin should be horizontal and all that jazz

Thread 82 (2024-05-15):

Propulsion board issues

JasonBrave, 2024-05-15:
MCLR silkscreen is at wrong side of programming header lmao

miles-milne, 2024-07-05:
R18, R20, R22, and R28 should be rated as "TBD" rather than 90mR

BluCodeGH, 2024-07-06:
CAN connector pinout is wrong. Also the pinout of the motor control gecko is unintuitive and should be improved.

BluCodeGH, 2024-07-08:
LEDs on the back are hard to see

miles-milne, 2024-07-09:
Wrong fuse footprints used. Should be an appropriate size for PTC fuses

miles-milne, 2024-07-09:
General board issues, including daisy chaining, via-in-pad, somewhat sus traces, and board is too large (too many components on the front side)

Closed 2025-05-31.

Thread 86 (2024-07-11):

Camera board issues

BluCodeGH, 2024-07-11:
VREF capacitor missing, and should just connect to VDDA anyways?

BluCodeGH, 2024-07-26:
Tie 12->2.8v buck en pin to 5v / vusb so that turning off bus 5v turns off cameras

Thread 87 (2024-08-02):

Remote Arming Issues

BluCodeGH, 2024-08-02:
- Silkscreens got removed from all the datamate connectors
- Buzzers interfere with mag switches, they need to be moved further away

BluCodeGH, 2024-08-02:
- PIC-controlled buzzer causes interference with the batt2 current measurement when on

Tessa-P, 2024-08-03:
Batt current sense should be called altimeter current sense (and numbered respectively)

StarlightDescender, 2025-08-11:
already fixed in new PR for 2026 but
- swap to geckos for consistency with new boards

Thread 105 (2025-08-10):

RPB issues

StarlightDescender, 2025-08-10:
Efuses tripping intermittently
Board is larger than it needs to be

StarlightDescender, 2025-08-10:
no ground planes on front/back of pcb

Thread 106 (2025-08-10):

novatel breakout issues

StarlightDescender, 2025-08-10:
20 pin connector footprint doesnt match part

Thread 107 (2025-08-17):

logger board issues

StarlightDescender, 2025-08-17:
- no way to tell how full SD card is without removing it

SAT-oO, 2025-08-17:
is it feasible to `f_size` then add?

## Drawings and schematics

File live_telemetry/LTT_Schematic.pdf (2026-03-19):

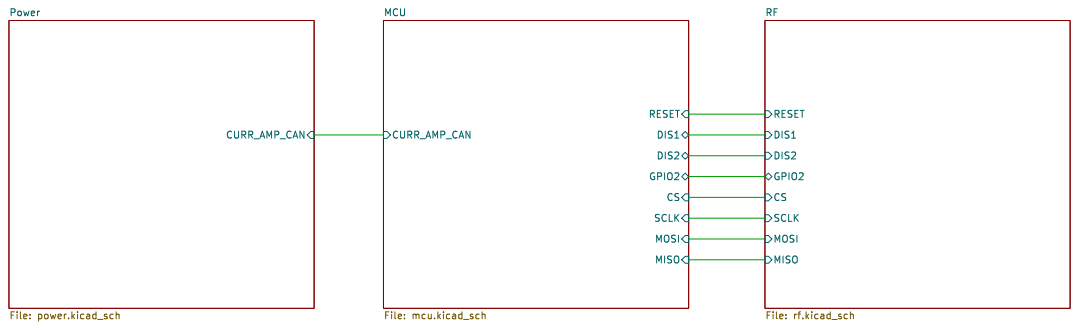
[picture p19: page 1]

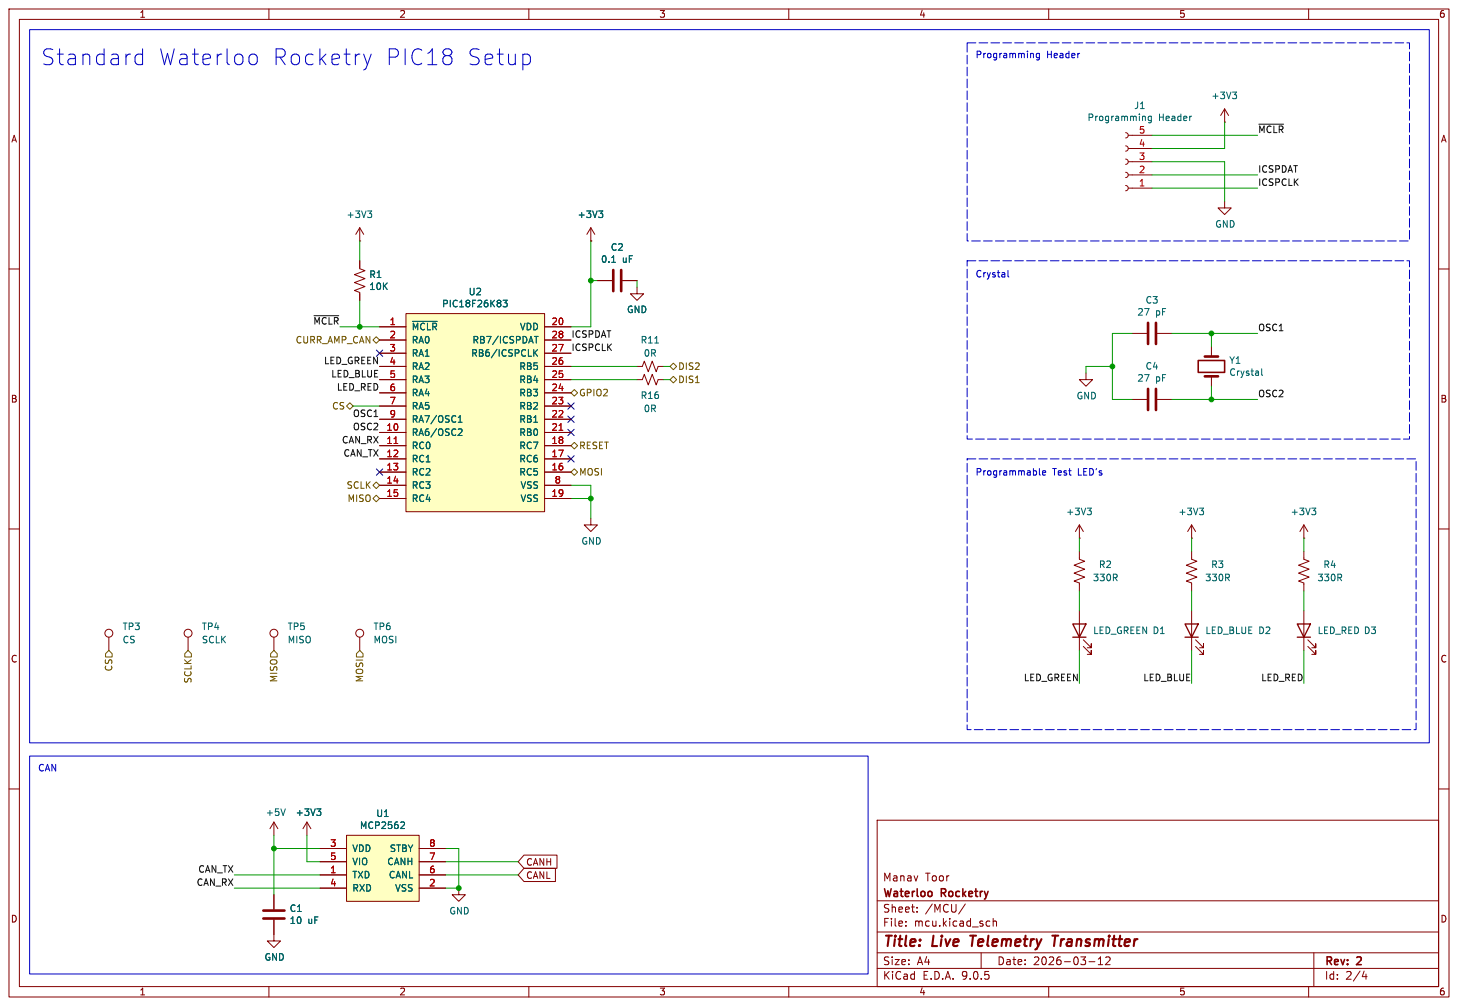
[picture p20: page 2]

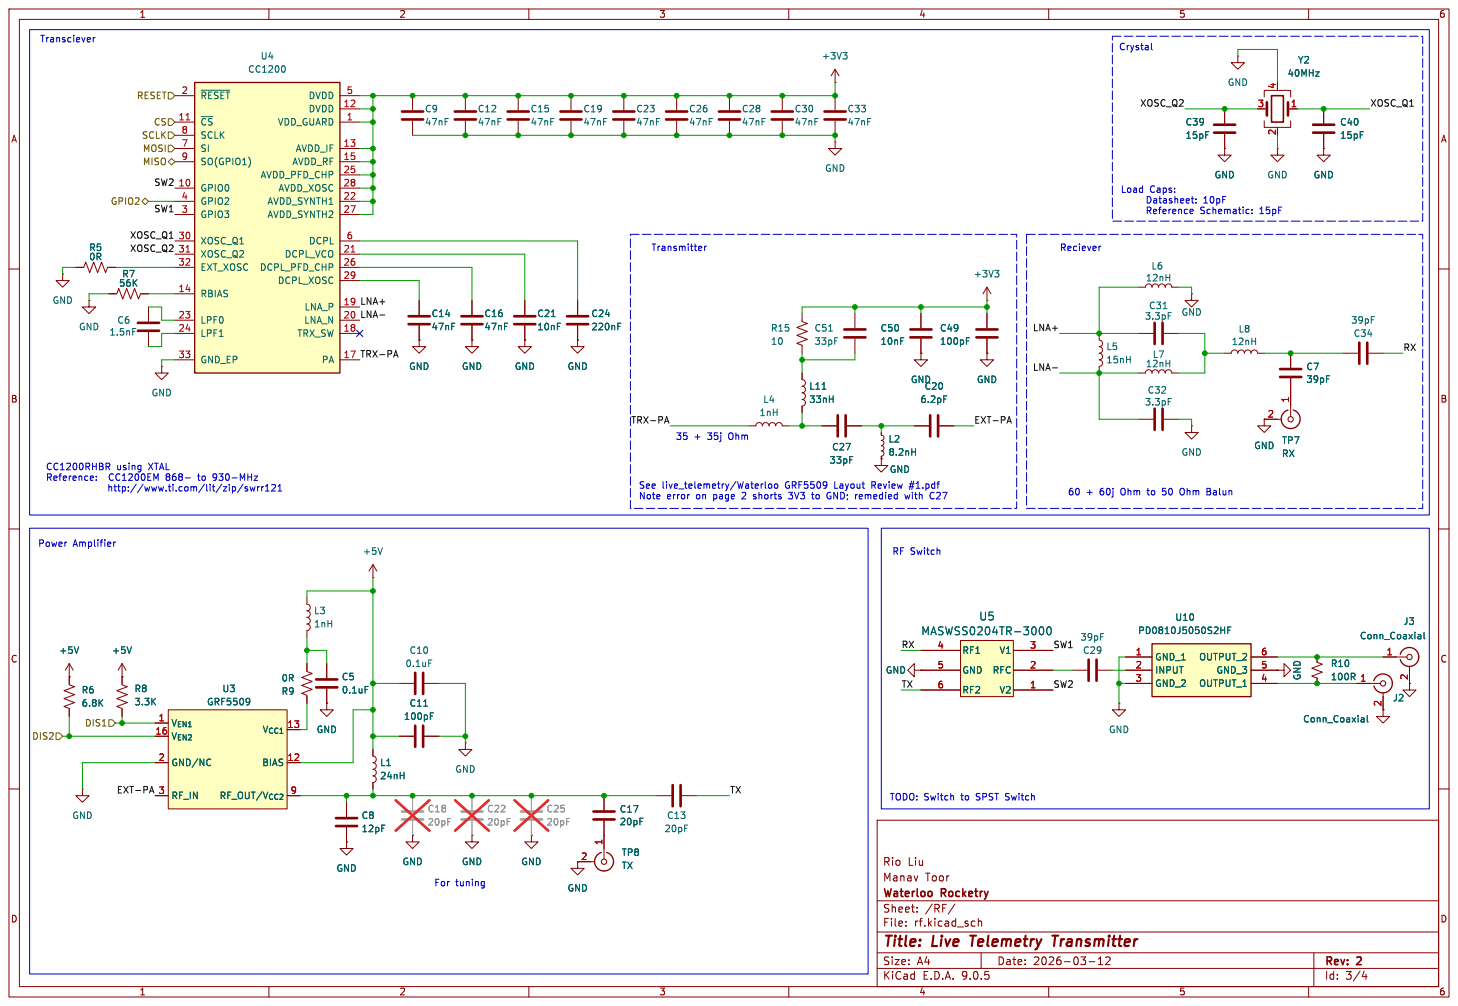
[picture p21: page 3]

2 R10 GND 100R U5 MASWSS0204TR-3000 RF1 4 GND 5 RF2 6 V1 3 RFC 2 V2 1 GND

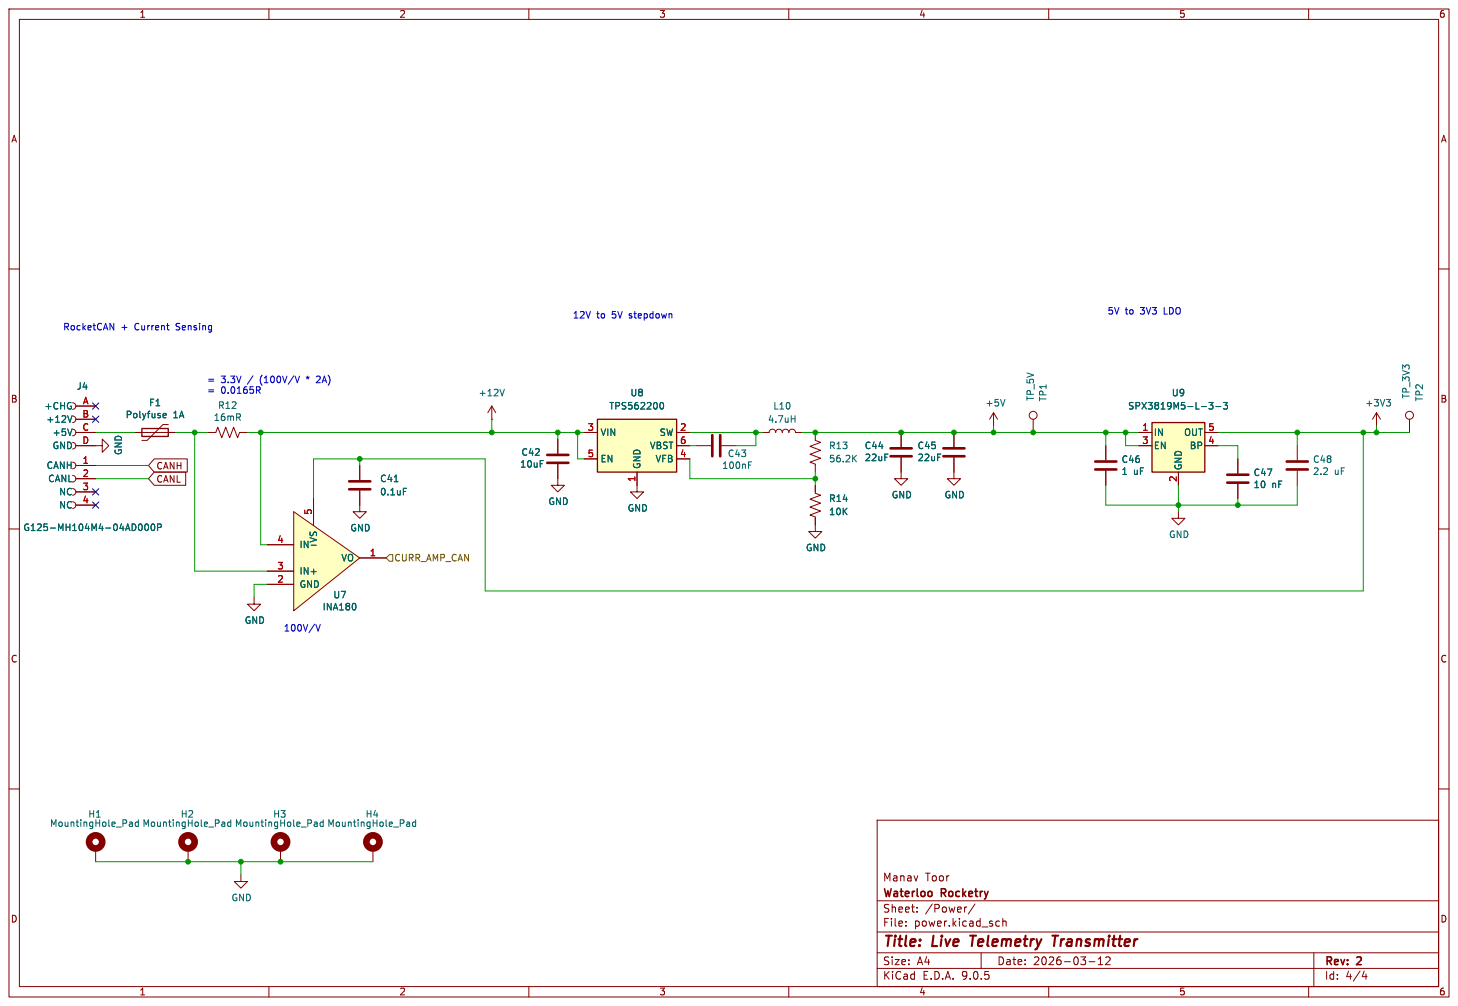
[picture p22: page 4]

1 SW 2 VBST 6 VFB 4 U8 TPS562200 GND GND GND

1 SW 2 VBST 6 VFB 4 GND

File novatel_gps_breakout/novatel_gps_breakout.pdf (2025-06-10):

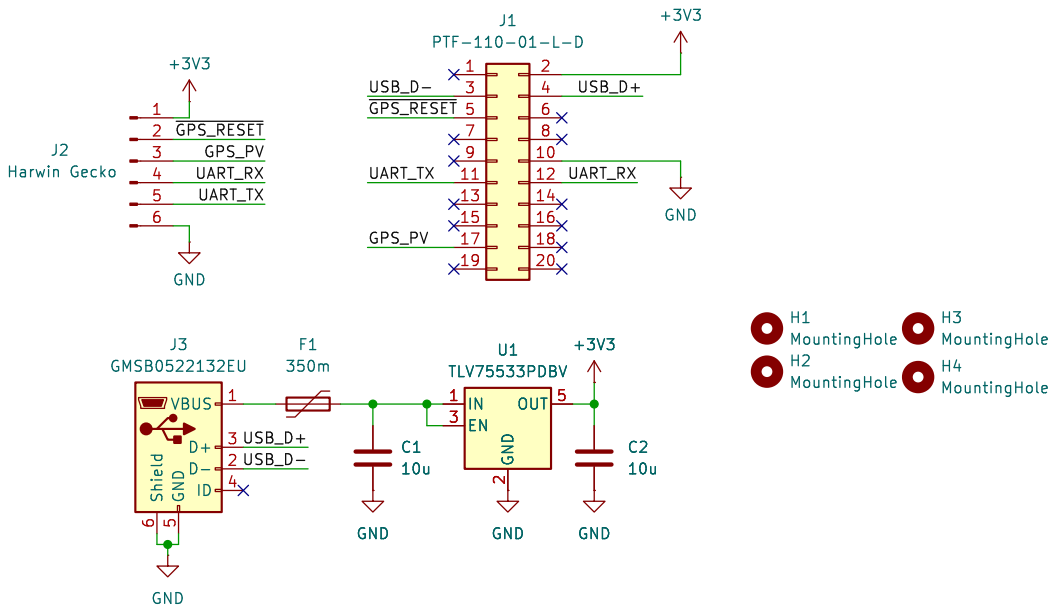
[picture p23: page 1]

Id: 1/1 Title: Novatel GNSS Reciever Breakout Board

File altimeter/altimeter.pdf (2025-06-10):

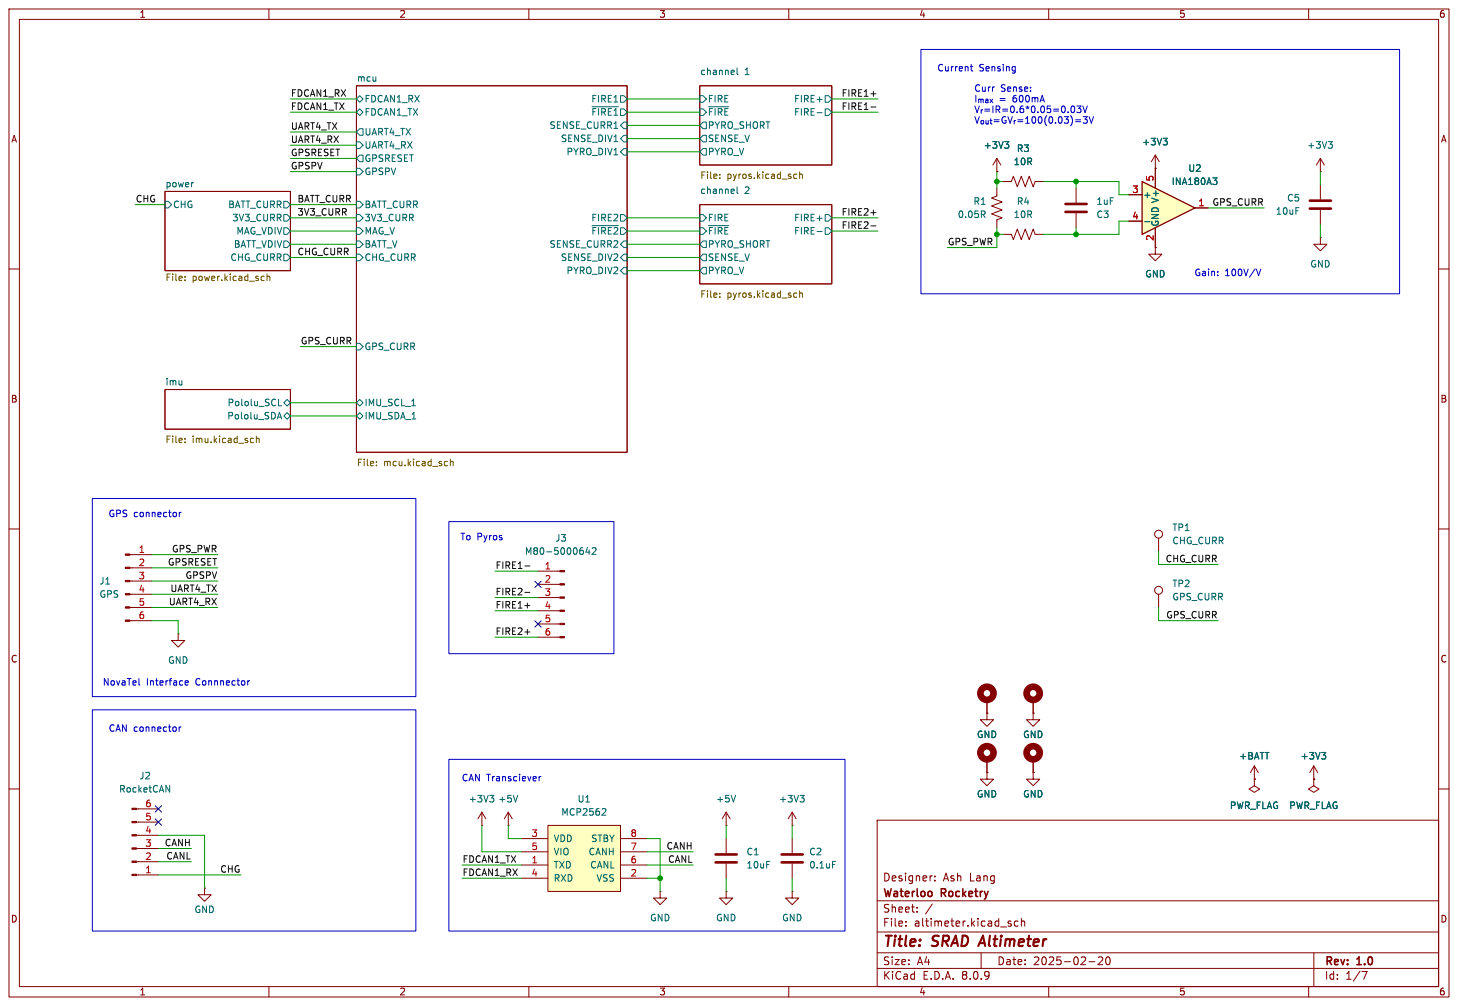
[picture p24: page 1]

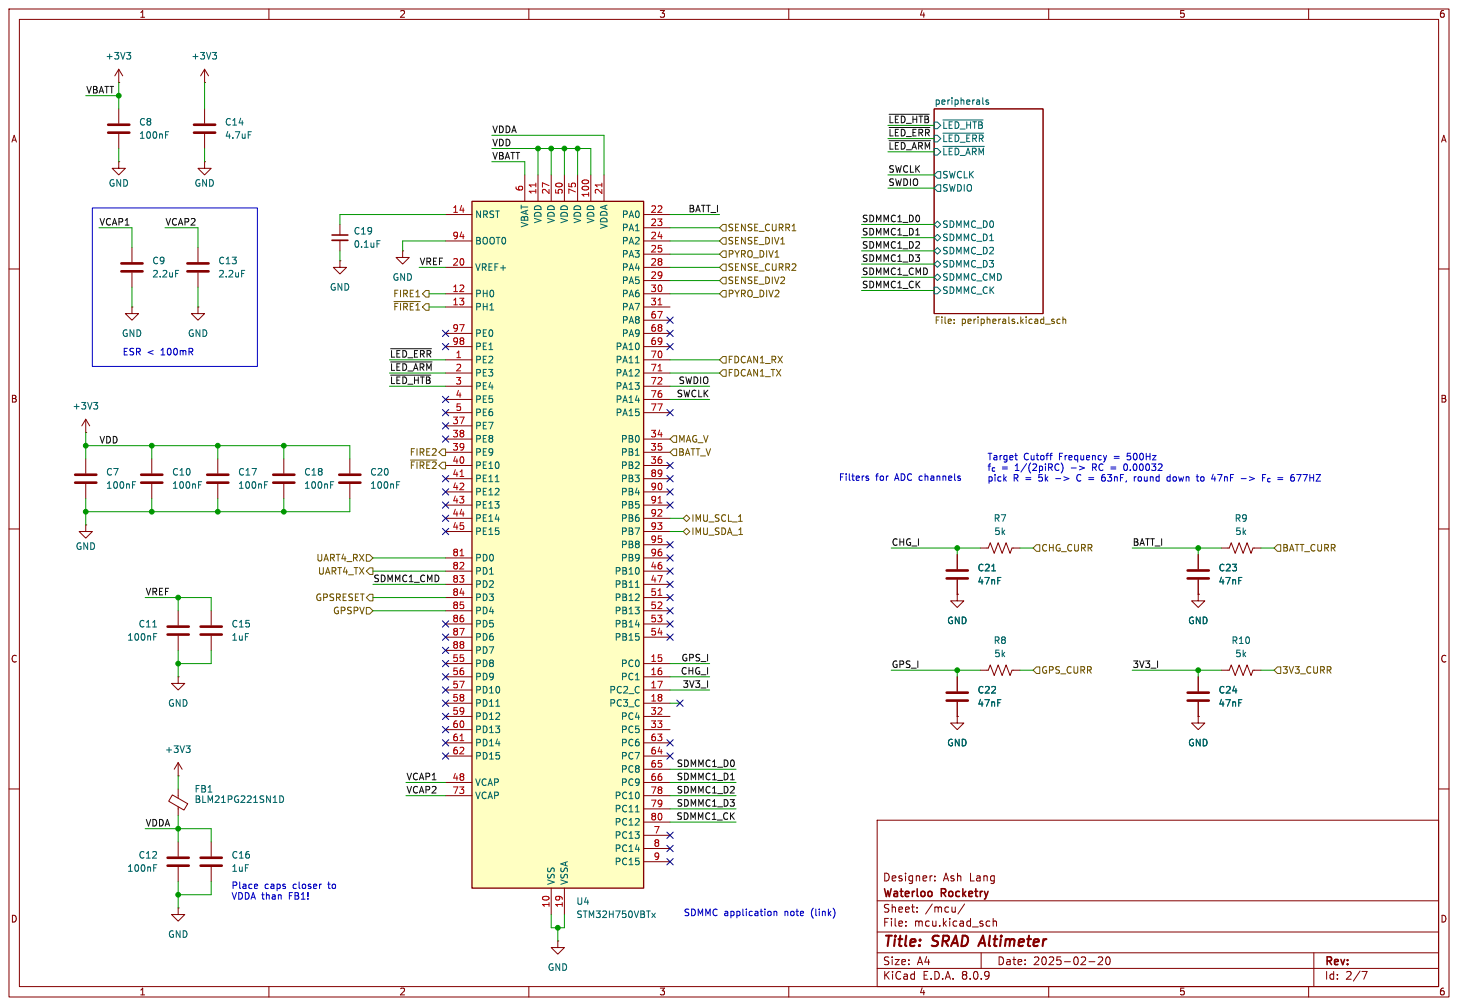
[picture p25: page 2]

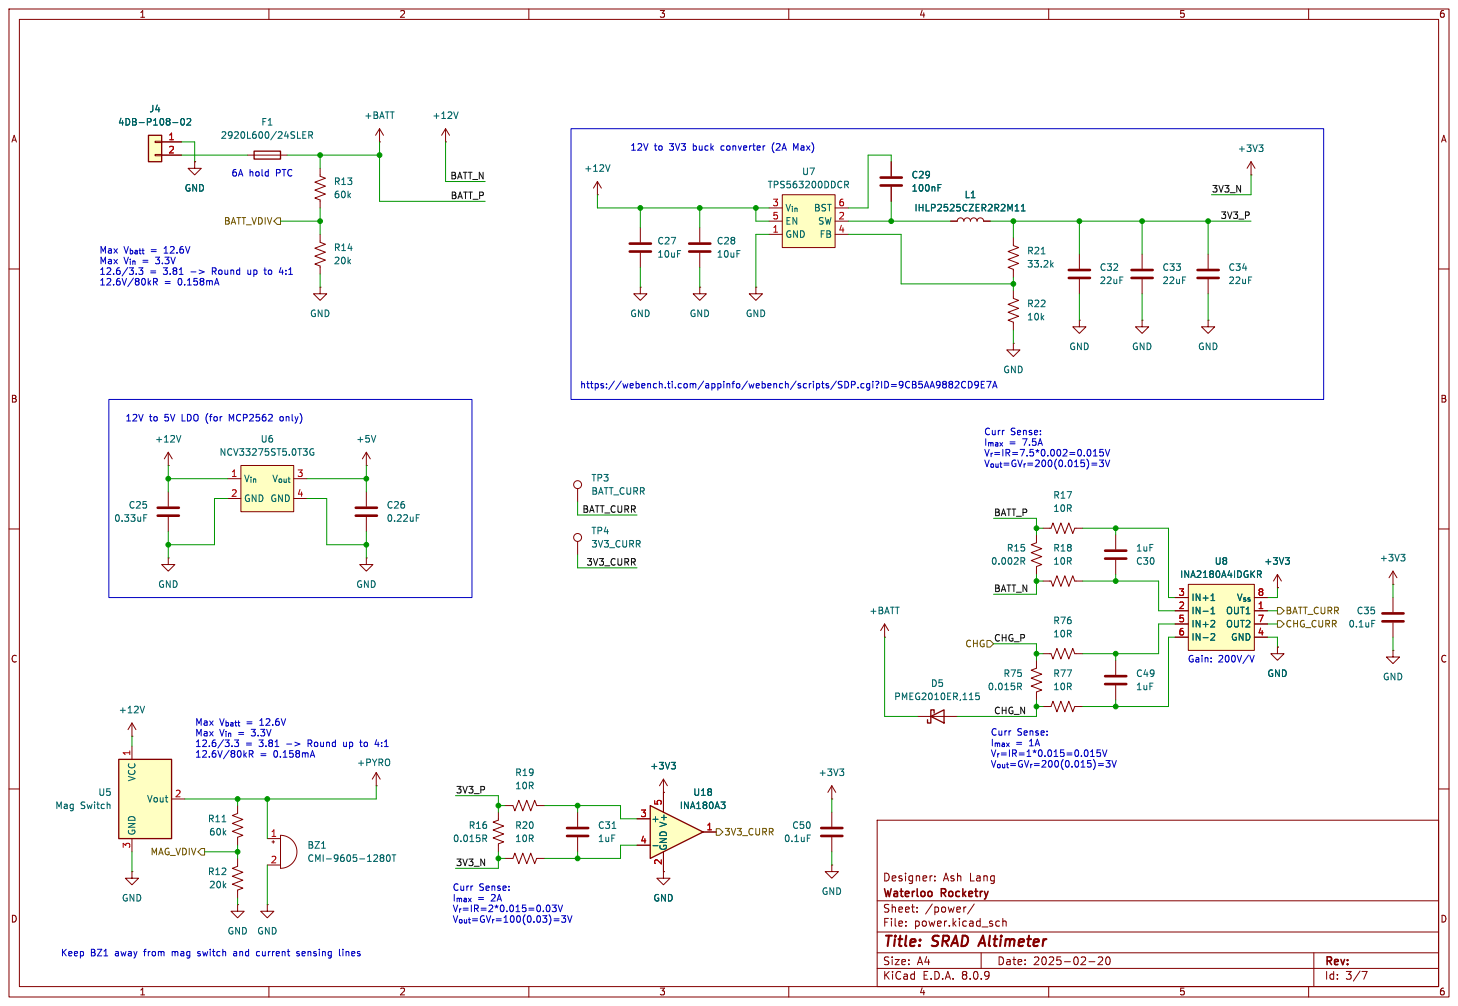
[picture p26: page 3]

6A hold PTC Max V_{batt}= 12.6V Max V_{in}= 3.3V

12V to 5V LDO (for MCP2562 only) Max V_{batt}= 12.6V Max V_{in}= 3.3V

https://webench.ti.com/appinfo/webench/scripts/SDP.cgi?ID=9CB5AA9882CD9E7A

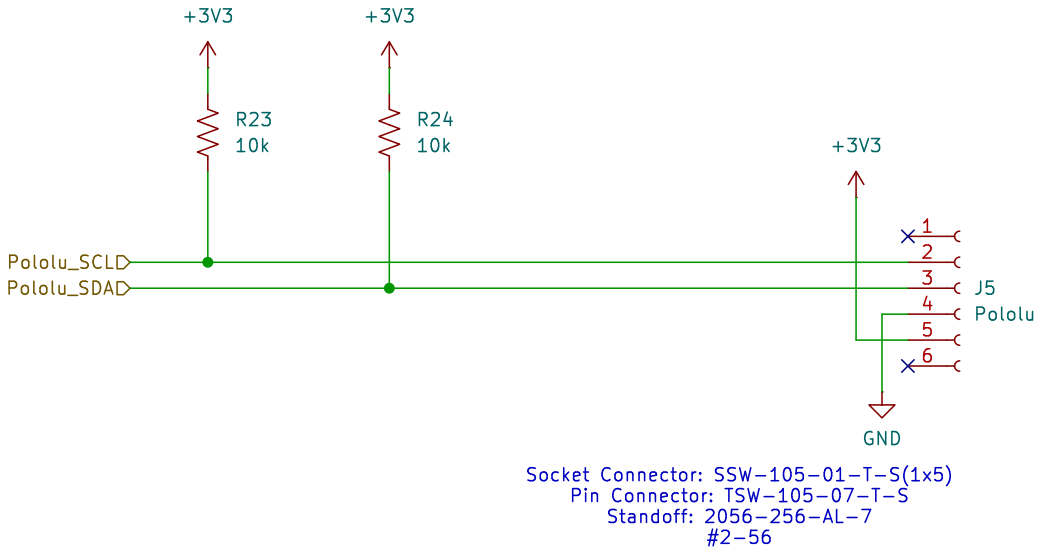
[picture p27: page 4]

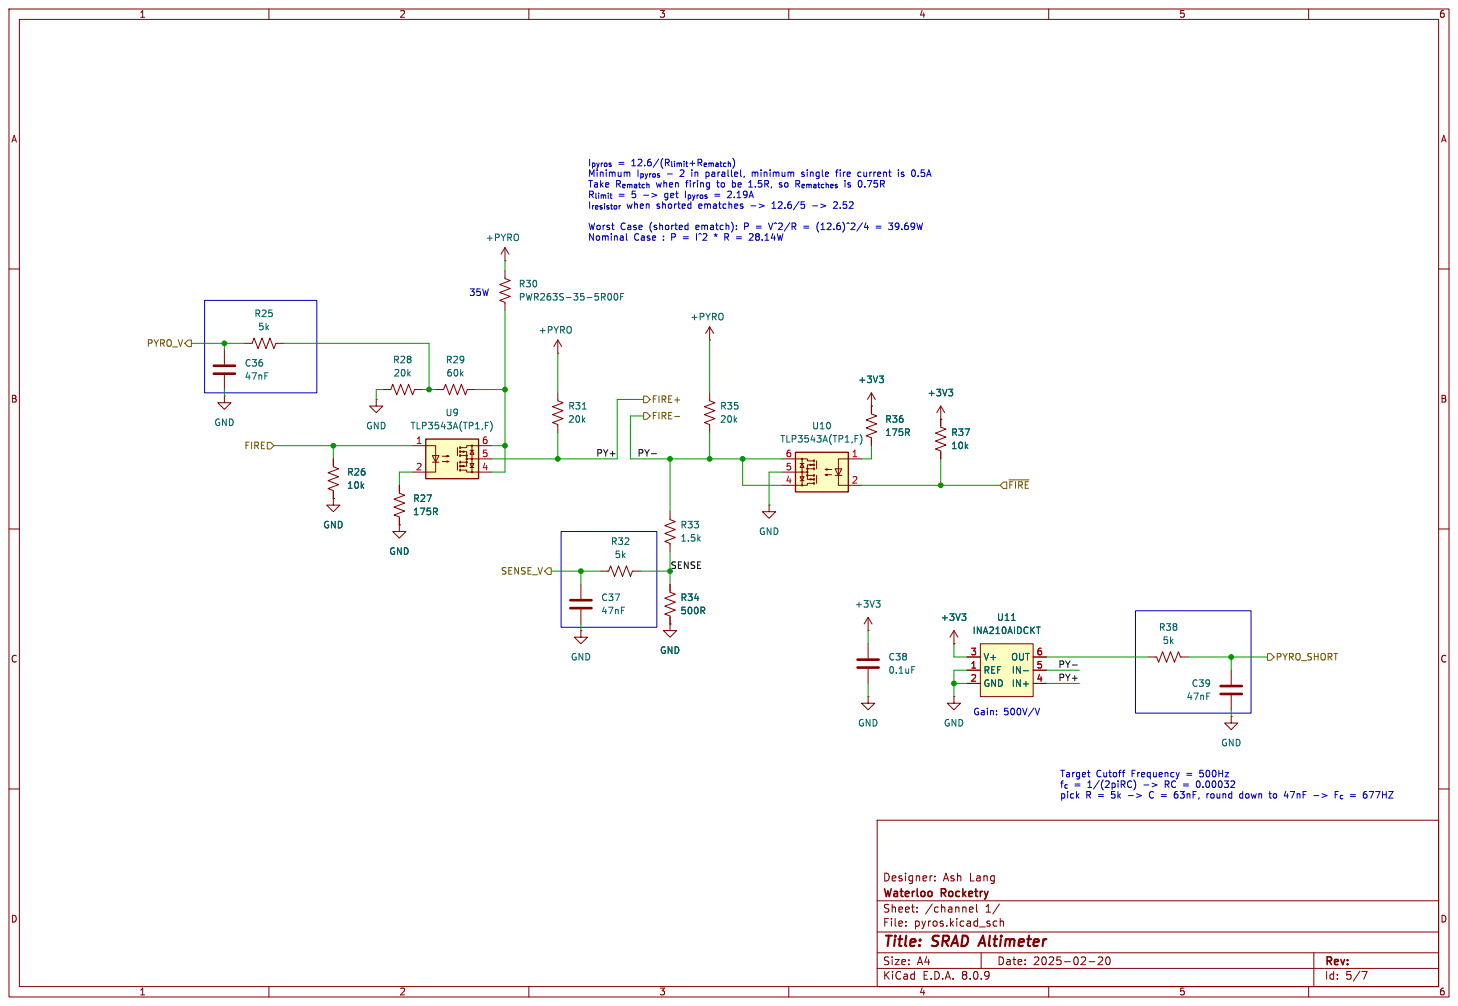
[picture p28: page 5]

Take R_{ematch}when firing to be 1.5R, so R_{ematches}is 0.75R

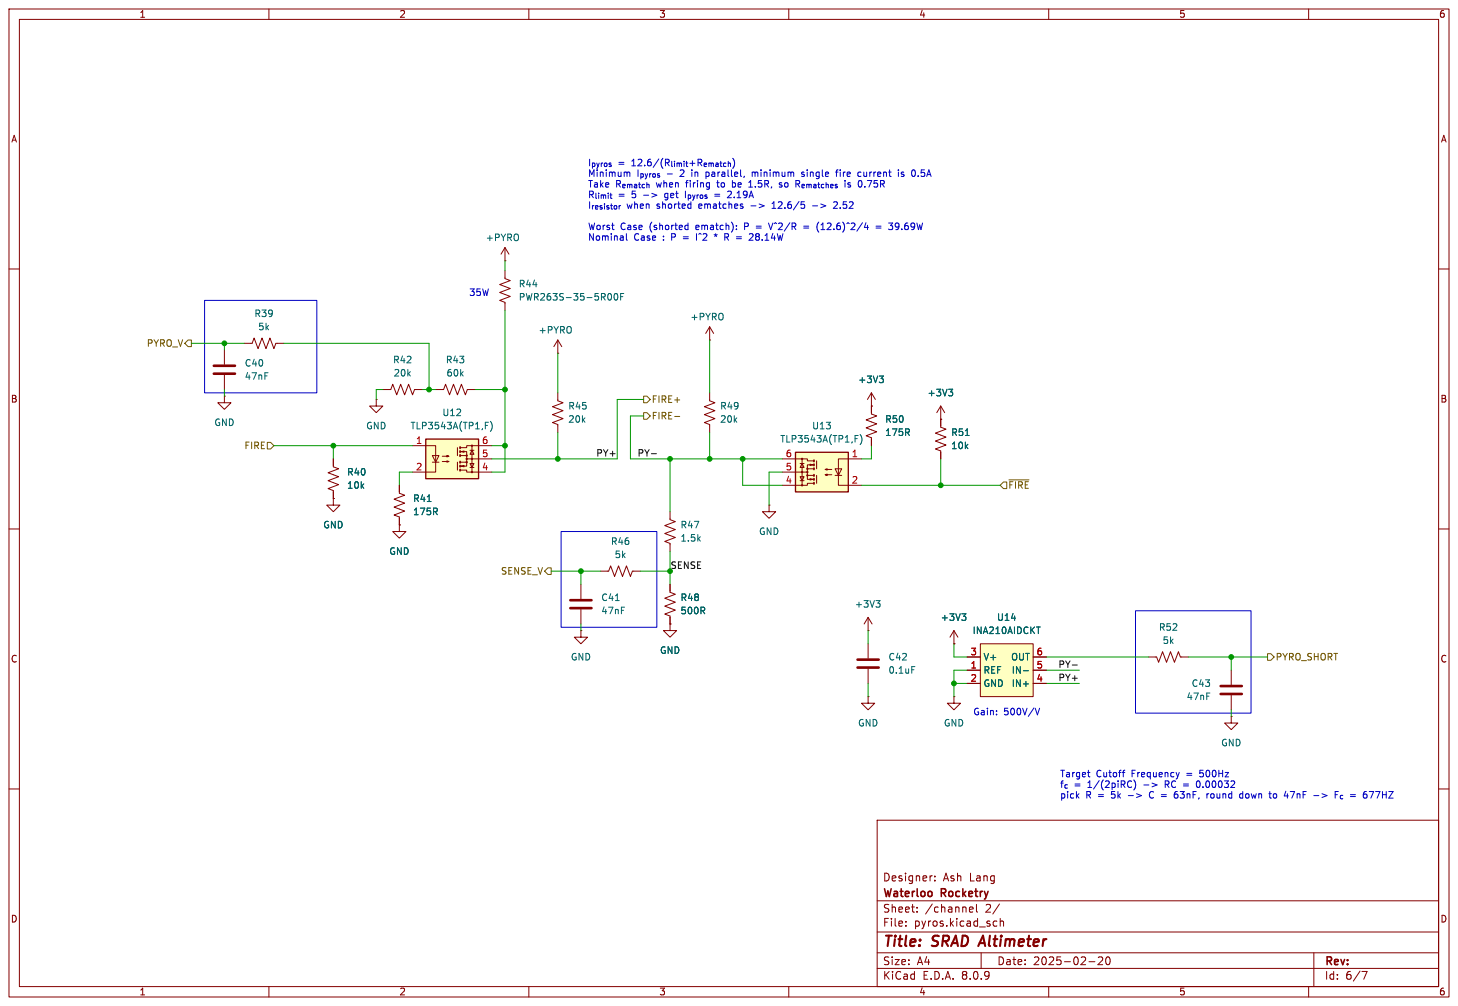
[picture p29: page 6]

Take R_{ematch}when firing to be 1.5R, so R_{ematches}is 0.75R

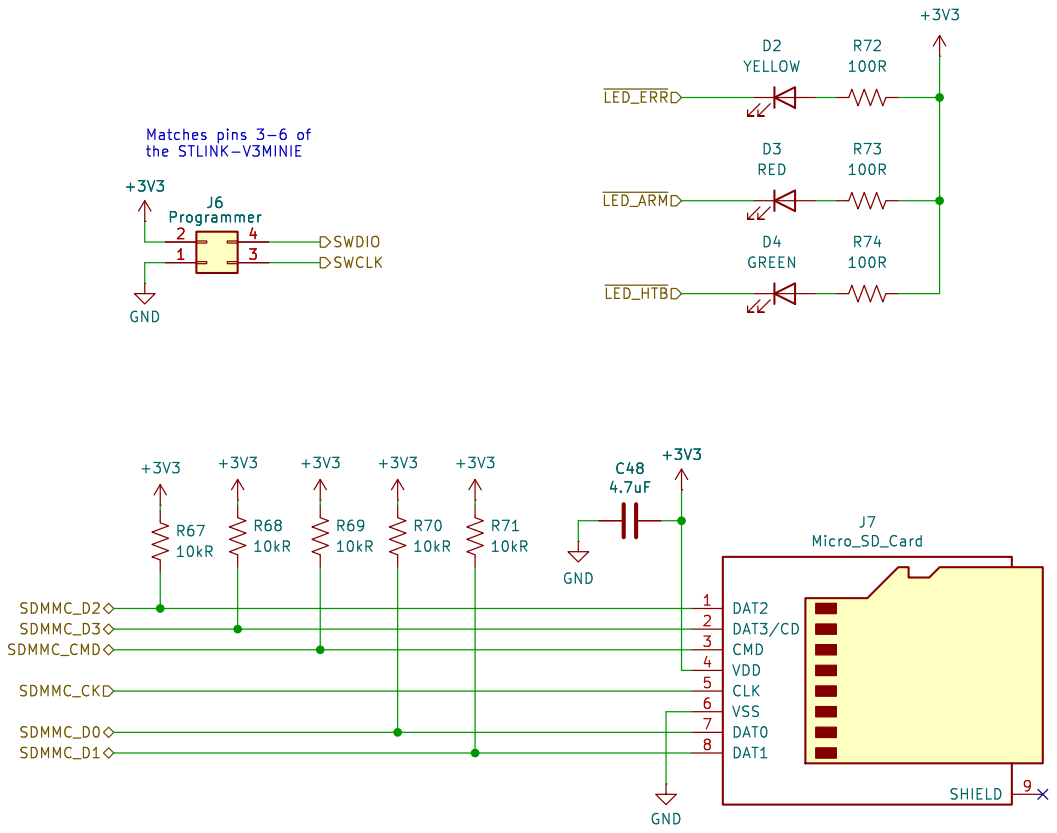
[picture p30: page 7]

Id: 7/7 Title: File: peripherals.kicad_sch Sheet: /mcu/peripherals/

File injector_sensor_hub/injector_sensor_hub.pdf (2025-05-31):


Id: 1/3 Title: Injector Sensor Hub


Id: 2/3 Title: Injector Sensor Hub


Optional Divider Stage R17 TBD

Id: 3/3 Title: Injector Sensor Hub




















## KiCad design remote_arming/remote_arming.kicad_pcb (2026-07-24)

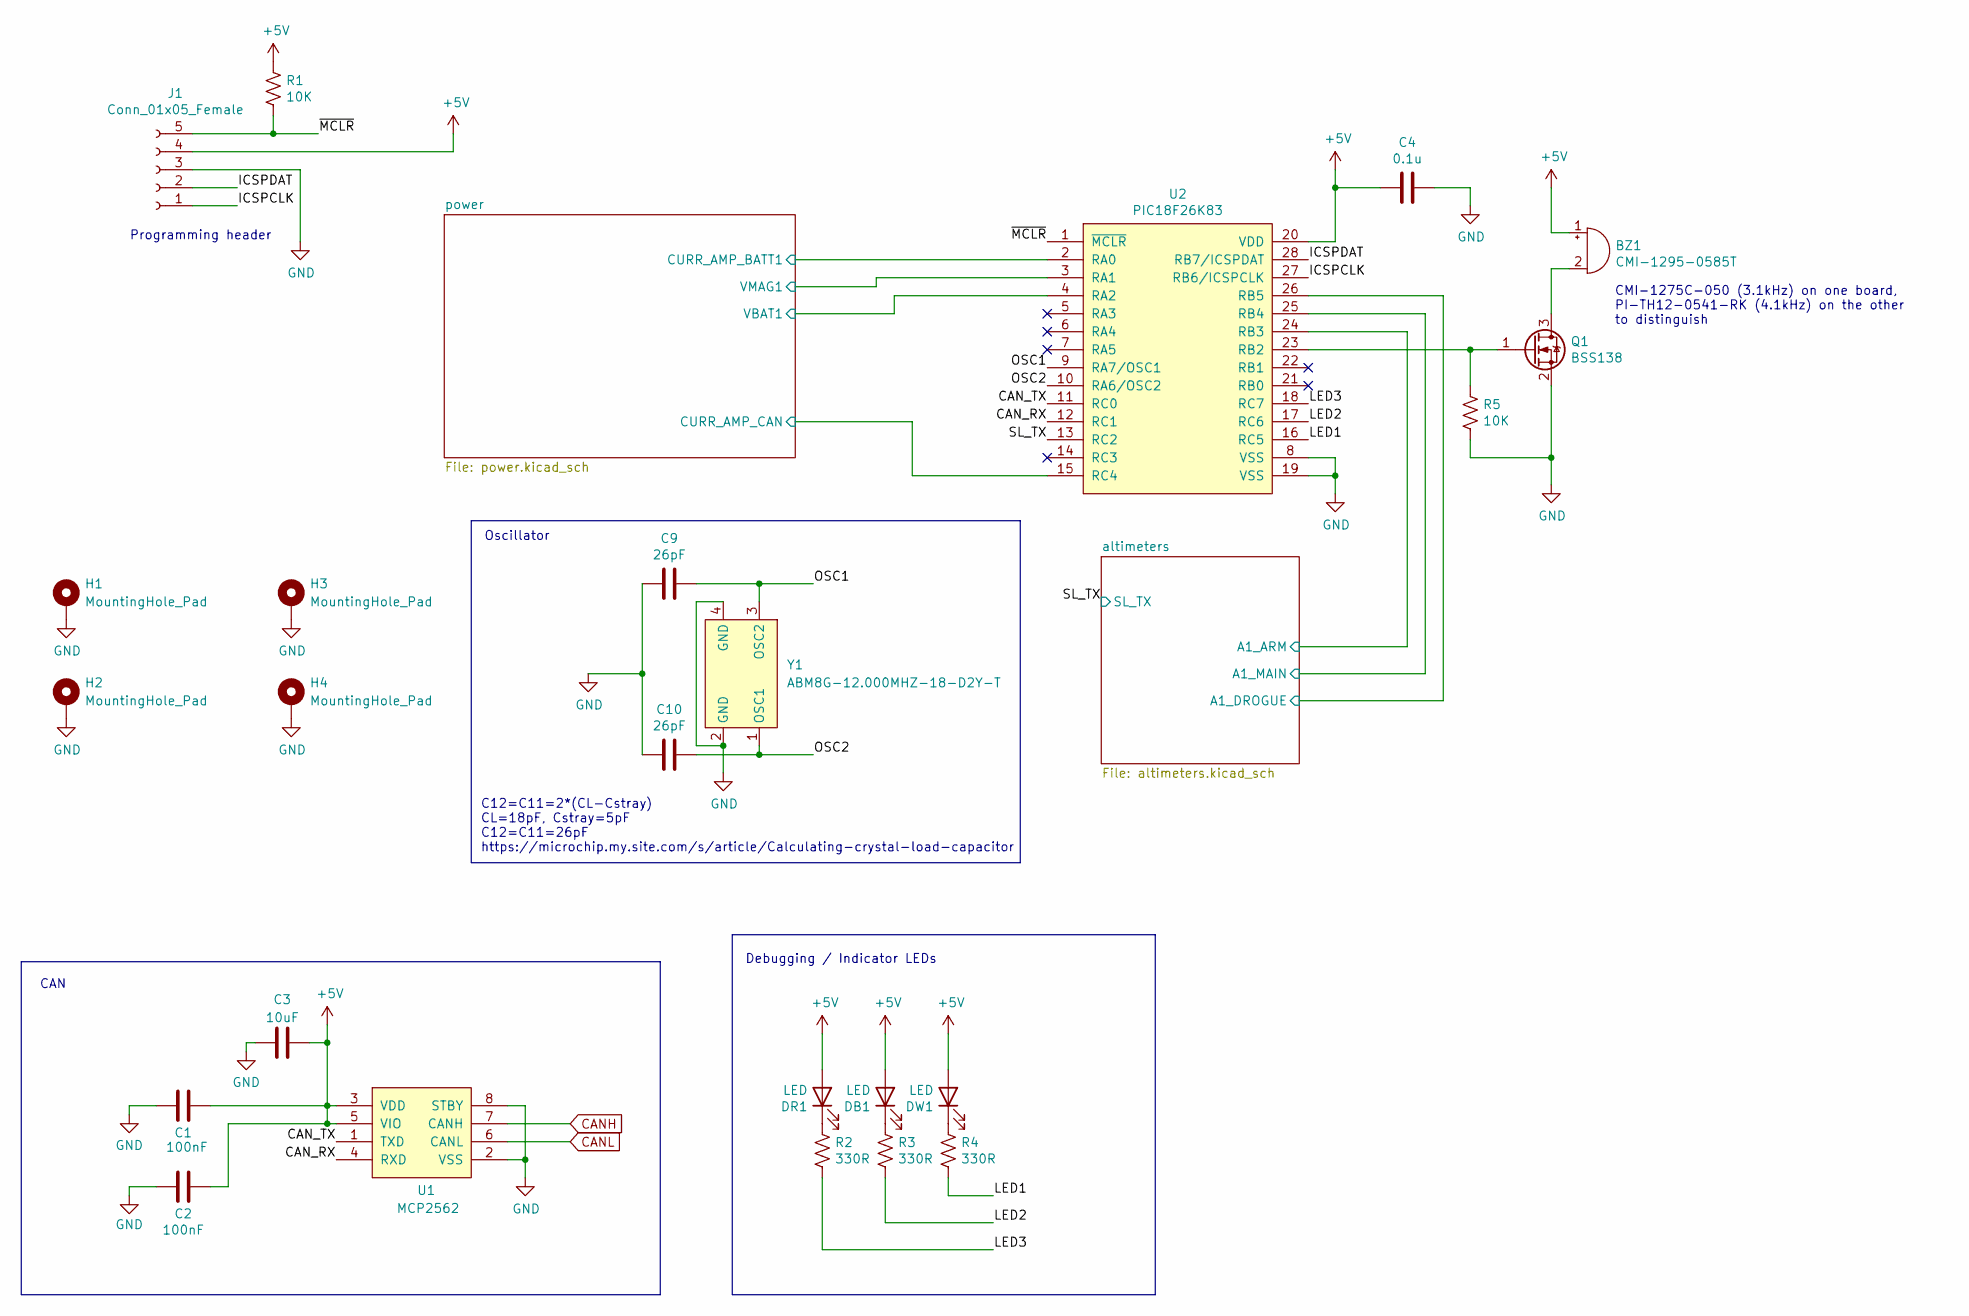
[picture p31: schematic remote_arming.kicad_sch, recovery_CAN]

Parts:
BZ1: CMI-1295-0585T; Buzzer_12x9.5RM7.6
C1, C2: 100nF; C_0603_1608Metric_Pad1.08x0.95mm_HandSolder
C3: 10uF; C_0603_1608Metric_Pad1.08x0.95mm_HandSolder
C4: 0.1u; C_0603_1608Metric_Pad1.08x0.95mm_HandSolder
C9: 26pF; C_0603_1608Metric
C10: 26pF; C_0603_1608Metric_Pad1.08x0.95mm_HandSolder
DB1: LED; LED_1206_3216Metric_Pad1.42x1.75mm_HandSolder
DR1: LED; LED_1206_3216Metric_Pad1.42x1.75mm_HandSolder
DW1: LED; LED_1206_3216Metric_Pad1.42x1.75mm_HandSolder
H1, H2, H3, H4: MountingHole_Pad; MountingHole_3.2mm_M3_Pad_TopBottom
J1: Conn_01x05_Female; PinSocket_5x2.54_SMD_90deg_952-3198-1-ND
Q1: BSS138; SOT-23_Handsoldering
R1, R5: 10K; R_0603_1608Metric_Pad0.98x0.95mm_HandSolder
R2, R3, R4: 330R; R_0603_1608Metric_Pad0.98x0.95mm_HandSolder
U1: MCP2562; SOIC-8_3.9x4.9mm_P1.27mm
U2: PIC18F26K83; SOIC-28W_7.5x18.7mm_P1.27mm
Y1: ABM8G-12.000MHZ-18-D2Y-T; Crystal_SMD_Abracon_ABM8G-4Pin_3.2x2.5mm

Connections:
+5V: BZ1.1 (-), C1.2, C2.1, C3.2, C4.2, DB1.2 (A), DR1.2 (A), DW1.2 (A), J1.4, R1.1, U1.3 (VDD), U1.5 (VIO), U2.20 (VDD); also elsewhere on the board
/CAN_RX: U1.4 (RXD), U2.12 (RC1)
/CAN_TX: U1.1 (TXD), U2.11 (RC0)
/ICSPCLK: J1.1, U2.27 (RB6/ICSPCLK)
/ICSPDAT: J1.2, U2.28 (RB7/ICSPDAT)
/LED1: R4.2, U2.16 (RC5)
/LED2: R3.2, U2.17 (RC6)
/LED3: R2.2, U2.18 (RC7)
/OSC1: C9.1, U2.9 (RA7/OSC1), Y1.3 (OSC2)
/OSC2: C10.1, U2.10 (RA6/OSC2), Y1.1 (OSC1)
/SL_TX: U2.13 (RC2); also elsewhere on the board
/altimeters/A1_ARM: U2.24 (RB3); also elsewhere on the board
/altimeters/A1_DROGUE: U2.26 (RB5); also elsewhere on the board
/altimeters/A1_MAIN: U2.25 (RB4); also elsewhere on the board
/power/CURR_AMP_BATT1: U2.2 (RA0); also elsewhere on the board
/power/CURR_AMP_CAN: U2.15 (RC4); also elsewhere on the board
/power/VBAT1: U2.4 (RA2); also elsewhere on the board
/power/VMAG1: U2.3 (RA1); also elsewhere on the board
/~MCLR: J1.5, R1.2, U2.1 (~MCLR)
CANH: U1.7 (CANH); also elsewhere on the board
CANL: U1.6 (CANL); also elsewhere on the board
GND: C1.1, C2.2, C3.1, C4.1, C9.2, C10.2, H1.1, H2.1, H3.1, H4.1, J1.3, Q1.2 (S), R5.2, U1.2 (VSS), U1.8 (STBY), U2.8 (VSS), U2.19 (VSS), Y1.2 (GND), Y1.4 (GND); also elsewhere on the board
unnamed: BZ1.2 (+), Q1.3 (D)
unnamed: DB1.1 (K), R3.1
unnamed: DR1.1 (K), R2.1
unnamed: DW1.1 (K), R4.1
unnamed: Q1.1 (G), R5.1, U2.23 (RB2)

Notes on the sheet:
Oscillator
Debugging / Indicator LEDs
CMI-1275C-050 (3.1kHz) on one board, PI-TH12-0541-RK (4.1kHz) on the other to distinguish
C12=C11=2*(CL-Cstray) CL=18pF, Cstray=5pF C12=C11=26pF https://microchip.my.site.com/s/article/Calculating-crystal-load-capacitor
CAN
Programming header

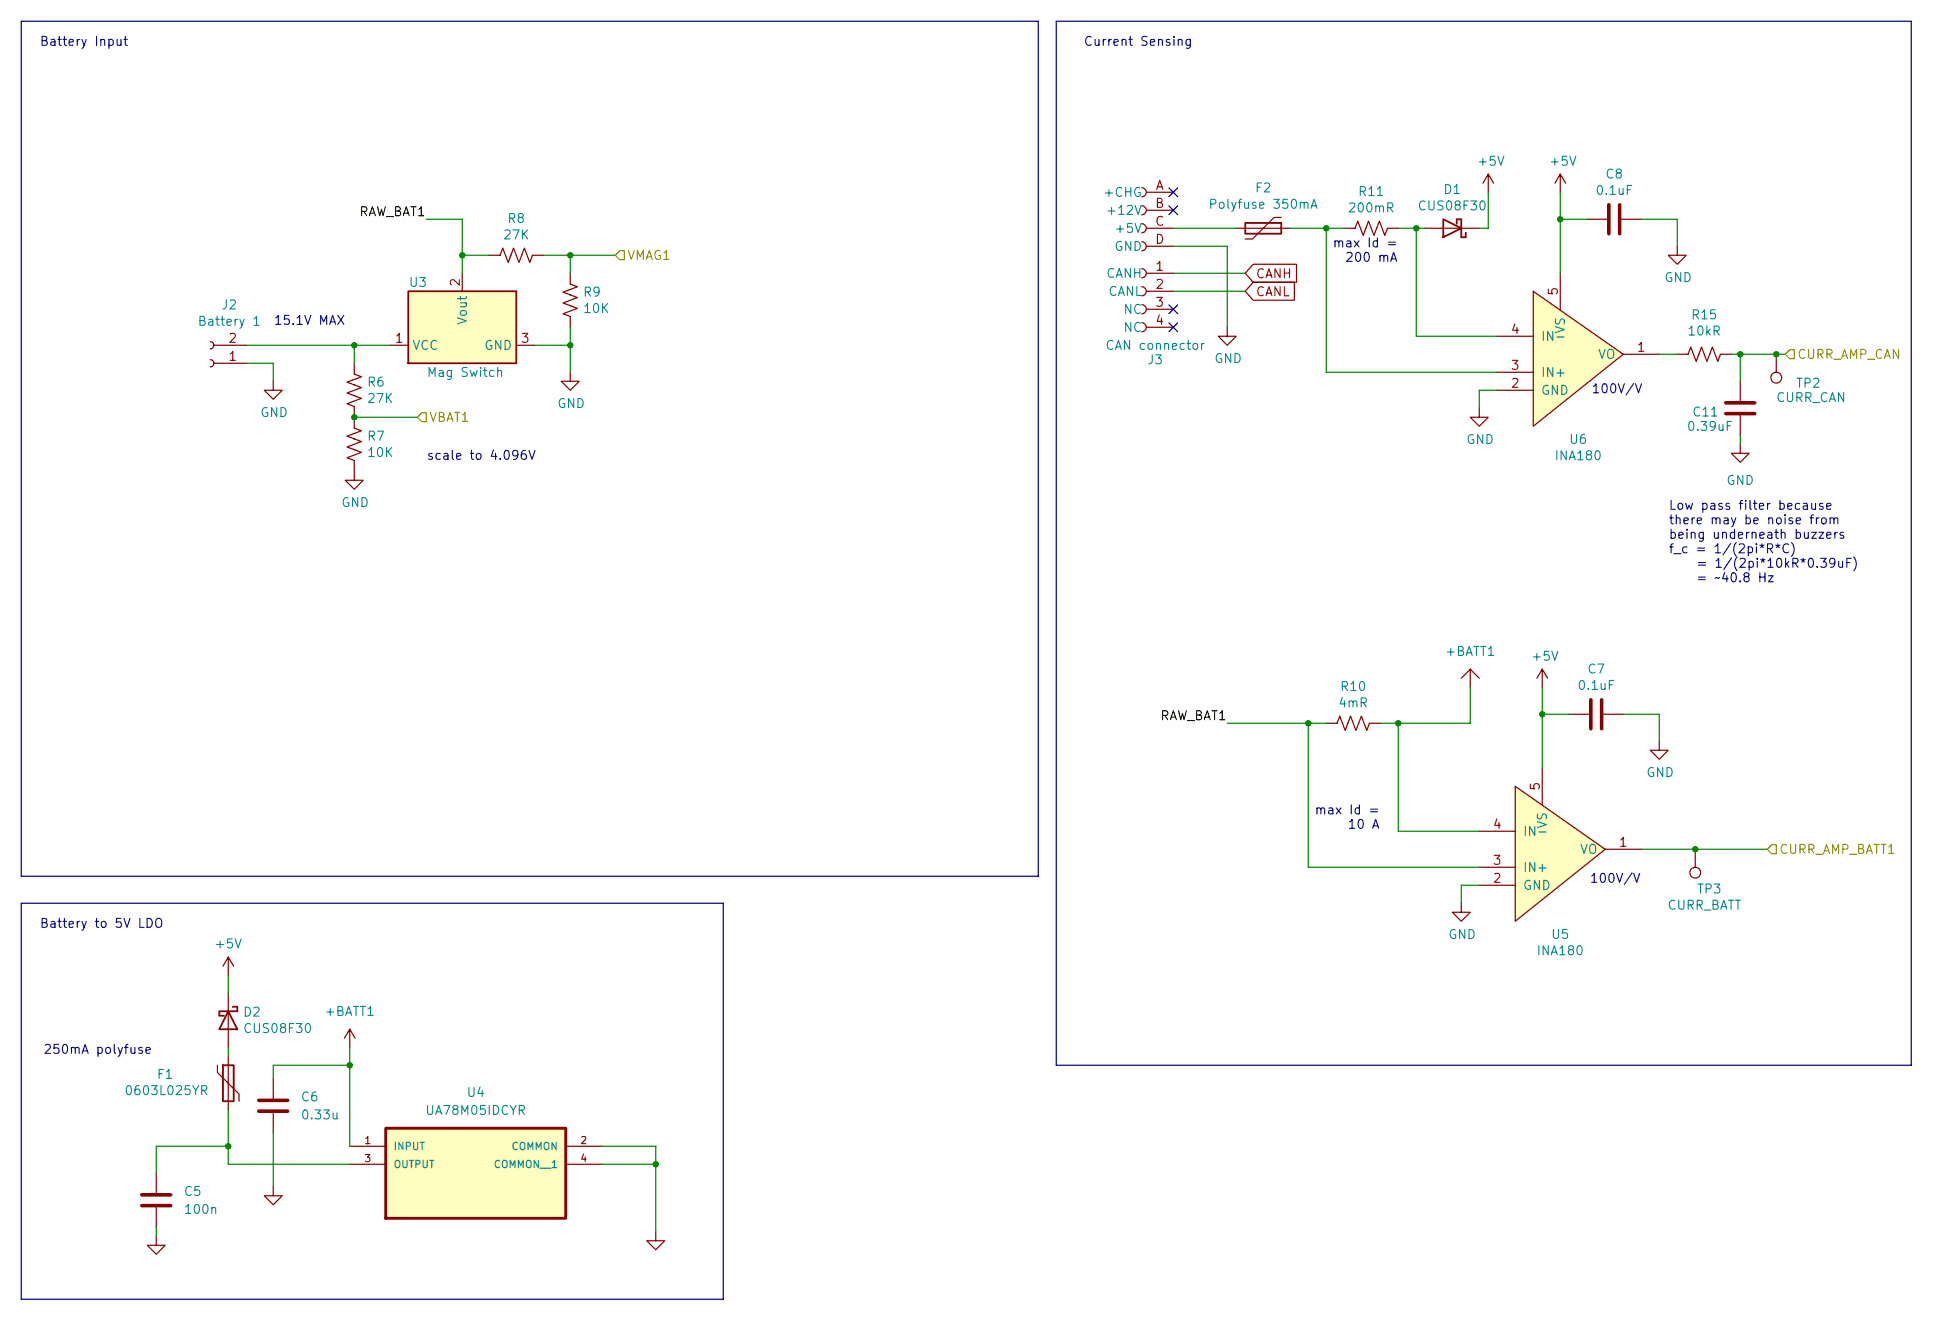
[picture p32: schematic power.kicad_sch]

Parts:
C5: 100n; C_0603_1608Metric_Pad1.08x0.95mm_HandSolder
C6: 0.33u; C_0603_1608Metric_Pad1.08x0.95mm_HandSolder
C7, C8: 0.1uF; C_0603_1608Metric_Pad1.08x0.95mm_HandSolder
C11: 0.39uF; C_0603_1608Metric_Pad1.08x0.95mm_HandSolder
D1, D2: CUS08F30; D_SOD-323_HandSoldering
F1: 0603L025YR; Fuse_0603_1608Metric_Pad1.05x0.95mm_HandSolder
F2: Polyfuse 350mA; Fuse_1206_3216Metric_Pad1.42x1.75mm_HandSolder
J2: Battery 1; BarrierBlock_ED2945-ND
J3: CAN connector; connector_Harwin_G125-MH104M4-04AD000P
R6, R8: 27K; R_0603_1608Metric_Pad0.98x0.95mm_HandSolder
R7, R9: 10K; R_0603_1608Metric_Pad0.98x0.95mm_HandSolder
R10: 4mR; R_1206_3216Metric_Pad1.30x1.75mm_HandSolder
R11: 200mR; R_0603_1608Metric_Pad0.98x0.95mm_HandSolder
R15: 10kR; R_0603_1608Metric_Pad0.98x0.95mm_HandSolder
TP2: CURR_CAN; TestPoint_Pad_D2.0mm
TP3: CURR_BATT; TestPoint_Pad_D2.0mm
U3: Mag Switch
U4: UA78M05IDCYR; SOT230P700X180-4N
U5, U6: INA180; SOT-23-5_HandSoldering

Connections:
+5V: C7.2, C8.2, D1.1 (K), D2.1 (K), U5.5 (VS), U6.5 (VS); also elsewhere on the board
+BATT1: C6.1, R10.1, U4.1 (INPUT), U5.4 (IN-); also elsewhere on the board
/power/CURR_AMP_BATT1: TP3.1, U5.1 (VO); also elsewhere on the board
/power/CURR_AMP_CAN: C11.1, R15.2, TP2.1; also elsewhere on the board
/power/RAW_BAT1: R8.2, R10.2, U3.2 (Vout), U5.3 (IN+)
/power/VBAT1: R6.2, R7.1; also elsewhere on the board
/power/VMAG1: R8.1, R9.1; also elsewhere on the board
CANH: J3.1 (CANH); also elsewhere on the board
CANL: J3.2 (CANL); also elsewhere on the board
GND: C5.2, C6.2, C7.1, C8.1, C11.2, J2.1, J3.D (GND), R7.2, R9.2, U3.3 (GND), U4.2 (COMMON), U4.4 (COMMON__1), U5.2 (GND), U6.2 (GND); also elsewhere on the board
unnamed: D1.2 (A), R11.1, U6.4 (IN-)
unnamed: D2.2 (A), F1.1
unnamed: J2.2, R6.1, U3.1 (VCC)
unnamed: F2.2, J3.C (+5V)
unnamed: C5.1, F1.2, U4.3 (OUTPUT)
unnamed: F2.1, R11.2, U6.3 (IN+)
unnamed: R15.1, U6.1 (VO)

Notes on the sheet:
100V/V
max Id = 200 mA
max Id = 10 A
Battery Input
250mA polyfuse
Current Sensing
Battery to 5V LDO
scale to 4.096V
Low pass filter because there may be noise from being underneath buzzers f_c = 1/(2pi*R*C) = 1/(2pi*10kR*0.39uF) = ~40.8 Hz
15.1V MAX

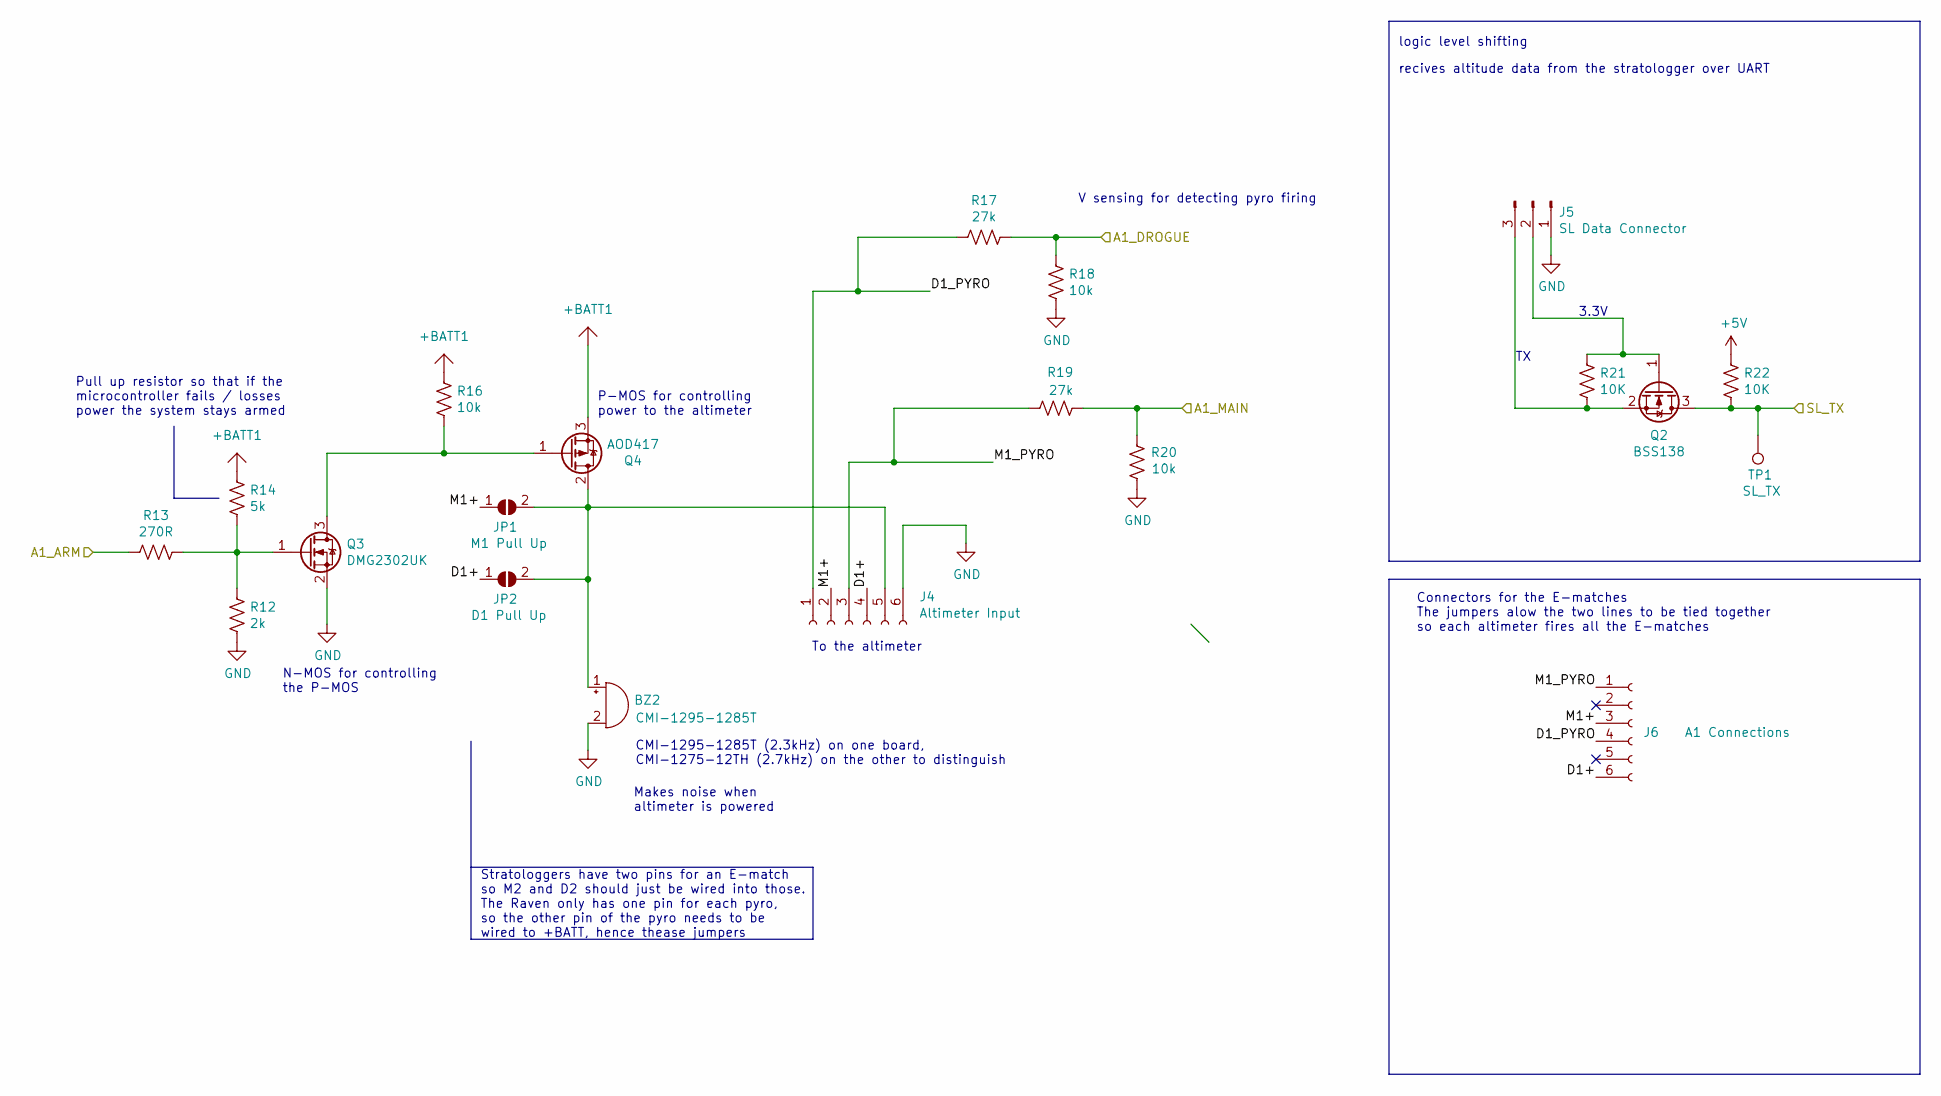
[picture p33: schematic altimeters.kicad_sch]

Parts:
BZ2: CMI-1295-1285T; Buzzer_12x9.5RM7.6
J4: Altimeter Input; connector_Harwin_G125–MG10605M4P
J5: SL Data Connector; JST_EH_S3B-EH_1x03_P2.50mm_Horizontal
J6: A1 Connections; connector_Harwin_G125–MG10605M4P
JP1: M1 Pull Up; SolderJumper-2_P1.3mm_Open_RoundedPad1.0x1.5mm
JP2: D1 Pull Up; SolderJumper-2_P1.3mm_Open_RoundedPad1.0x1.5mm
Q2: BSS138; SOT-23_Handsoldering
Q3: DMG2302UK; SOT-23_Handsoldering
Q4: AOD417; TO-252-2
R12: 2k; R_0603_1608Metric_Pad0.98x0.95mm_HandSolder
R13: 270R; R_0603_1608Metric_Pad0.98x0.95mm_HandSolder
R14: 5k; R_0603_1608Metric_Pad0.98x0.95mm_HandSolder
R16, R18, R20: 10k; R_0603_1608Metric_Pad0.98x0.95mm_HandSolder
R17, R19: 27k; R_0603_1608Metric_Pad0.98x0.95mm_HandSolder
R21, R22: 10K; R_0603_1608Metric_Pad0.98x0.95mm_HandSolder
TP1: SL_TX; TestPoint_Pad_D2.0mm

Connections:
+5V: R22.1; also elsewhere on the board
+BATT1: Q4.3 (S), R14.1, R16.1; also elsewhere on the board
/SL_TX: Q2.3 (D), R22.2, TP1.1; also elsewhere on the board
/altimeters/A1_ARM: R13.2; also elsewhere on the board
/altimeters/A1_DROGUE: R17.1, R18.2; also elsewhere on the board
/altimeters/A1_MAIN: R19.2, R20.2; also elsewhere on the board
/altimeters/D1+: J4.4, J6.6, JP2.1 (A)
/altimeters/D1_PYRO: J4.1, J6.4, R17.2
/altimeters/M1+: J4.2, J6.3, JP1.1 (A)
/altimeters/M1_PYRO: J4.3, J6.1, R19.1
GND: BZ2.2 (+), J4.6, J5.1, Q3.2 (S), R12.2, R18.1, R20.1; also elsewhere on the board
unnamed: BZ2.1 (-), J4.5, JP1.2 (B), JP2.2 (B), Q4.2 (D)
unnamed: J5.2, Q2.1 (G), R21.1
unnamed: J5.3, Q2.2 (S), R21.2
unnamed: Q3.3 (D), Q4.1 (G), R16.2
unnamed: Q3.1 (G), R12.1, R13.1, R14.2

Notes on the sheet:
To the altimeter
N-MOS for controlling the P-MOS
logic level shifting
CMI-1295-1285T (2.3kHz) on one board, CMI-1275-12TH (2.7kHz) on the other to distinguish
P-MOS for controlling power to the altimeter
3.3V
recives altitude data from the stratologger over UART
Pull up resistor so that if the microcontroller fails / losses power the system stays armed
Stratologgers have two pins for an E-match so M2 and D2 should just be wired into those. The Raven only has one pin for each pyro, so the other pin of the pyro needs to be wired to +BATT, hence thease jumpers
V sensing for detecting pyro firing
Connectors for the E-matches The jumpers alow the two lines to be tied together so each altimeter fires all the E-matches
Makes noise when altimeter is powered

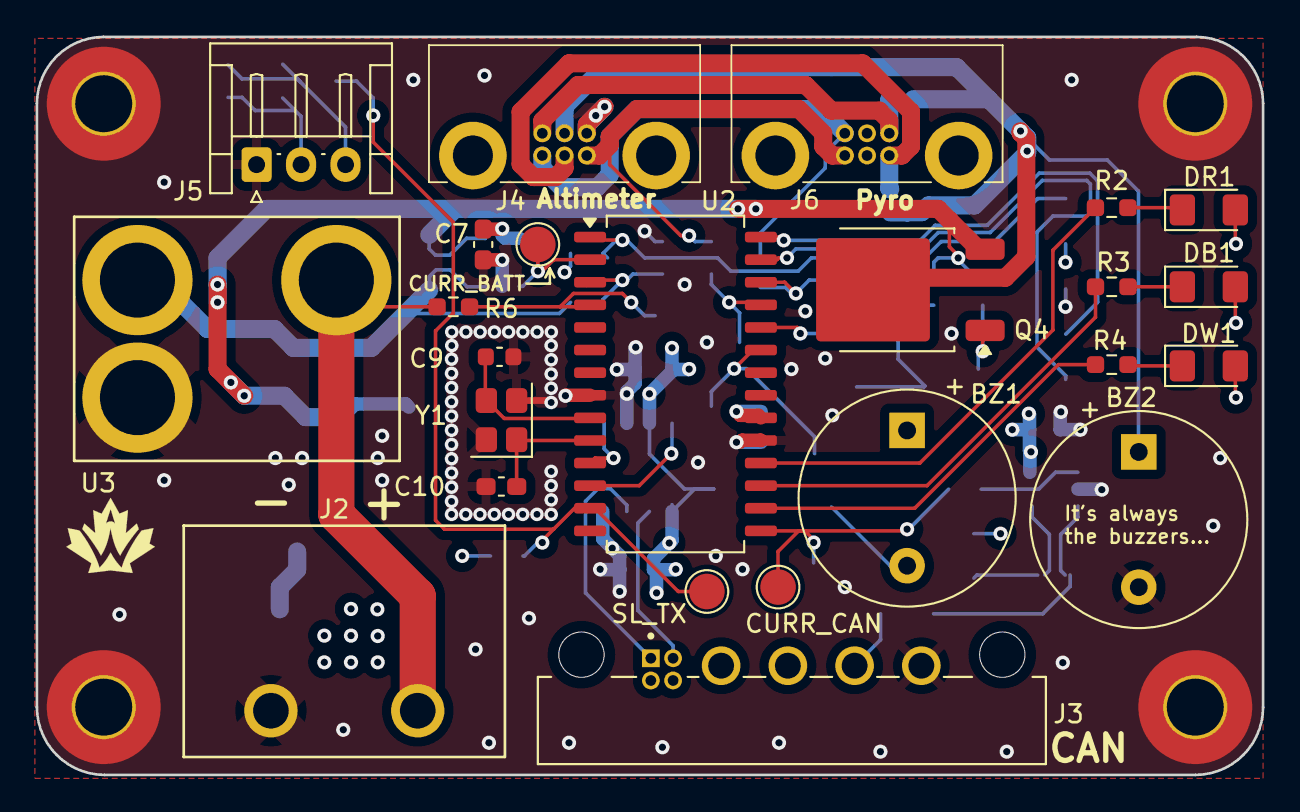
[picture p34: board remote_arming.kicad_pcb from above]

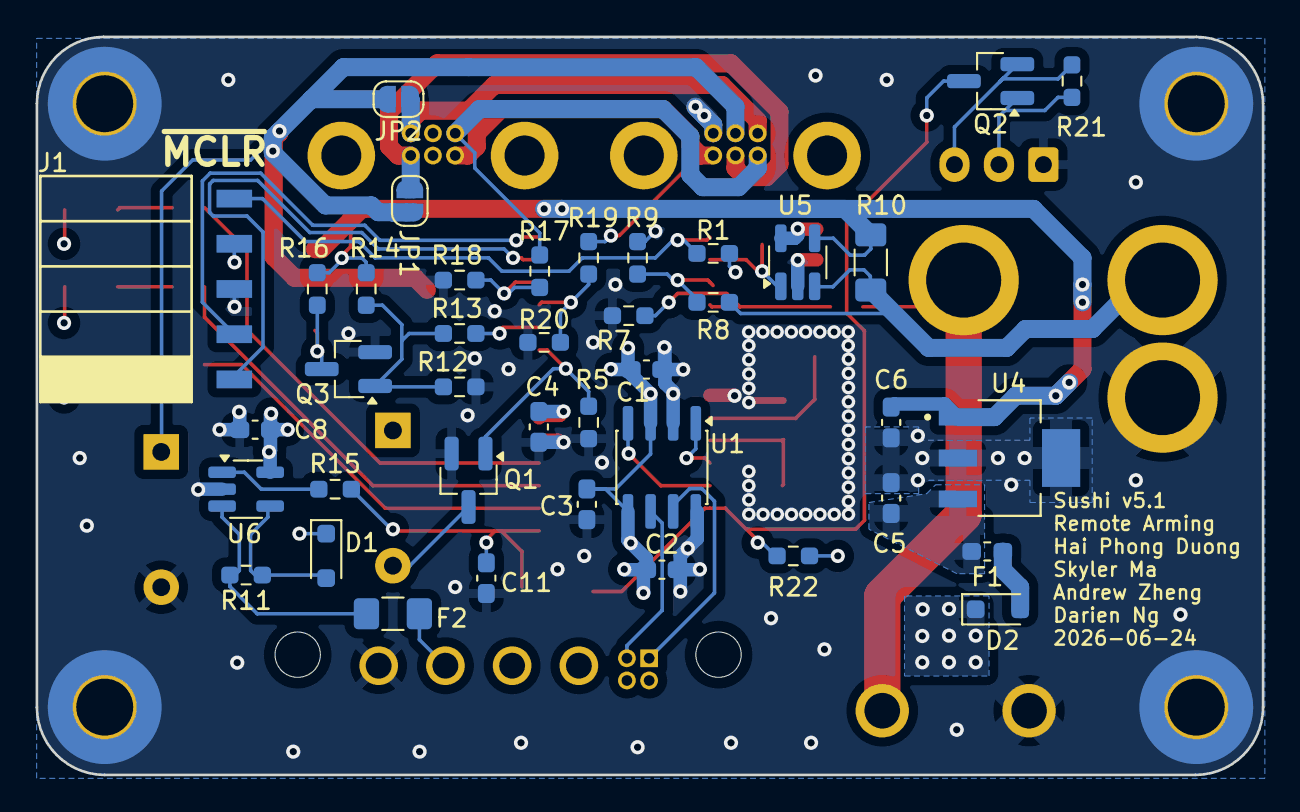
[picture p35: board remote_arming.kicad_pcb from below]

Board: 4 copper layers, 68.9 x 41.5 mm, 68 parts (40 on the bottom side), 45 nets.

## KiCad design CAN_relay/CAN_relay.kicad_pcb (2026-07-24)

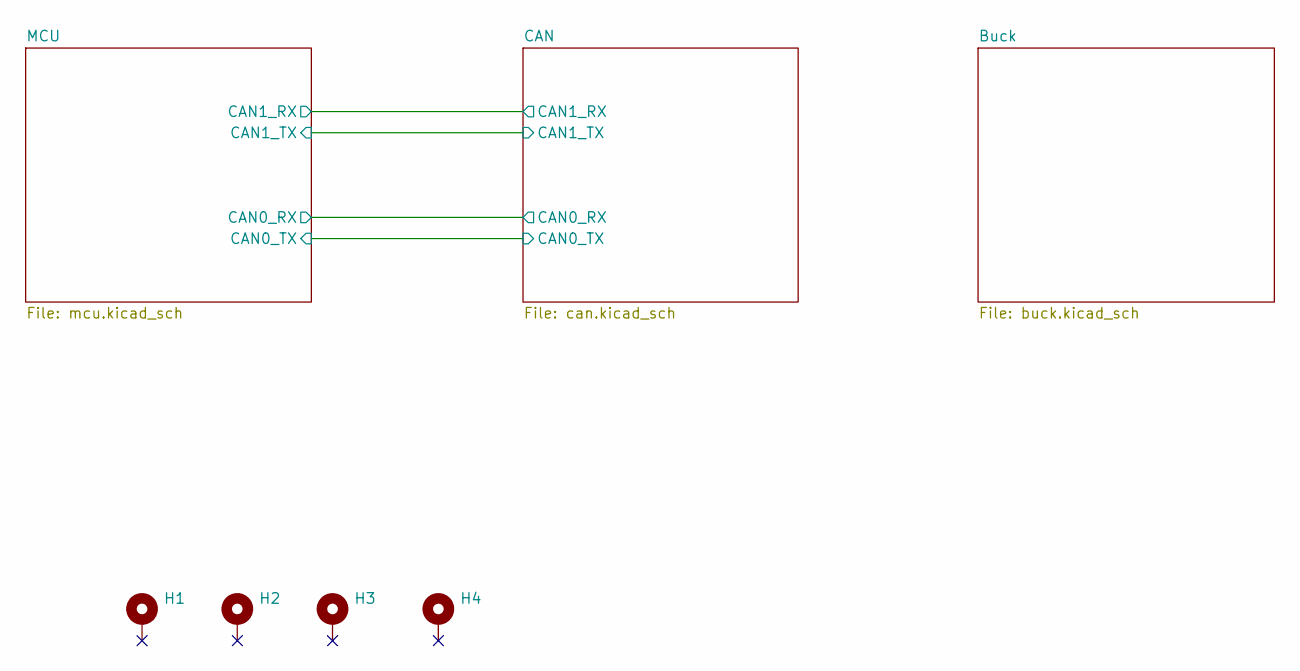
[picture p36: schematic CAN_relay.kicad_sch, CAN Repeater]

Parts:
H1, H2, H3, H4: MountingHole_Pad; MountingHole_3.2mm_M3_Pad

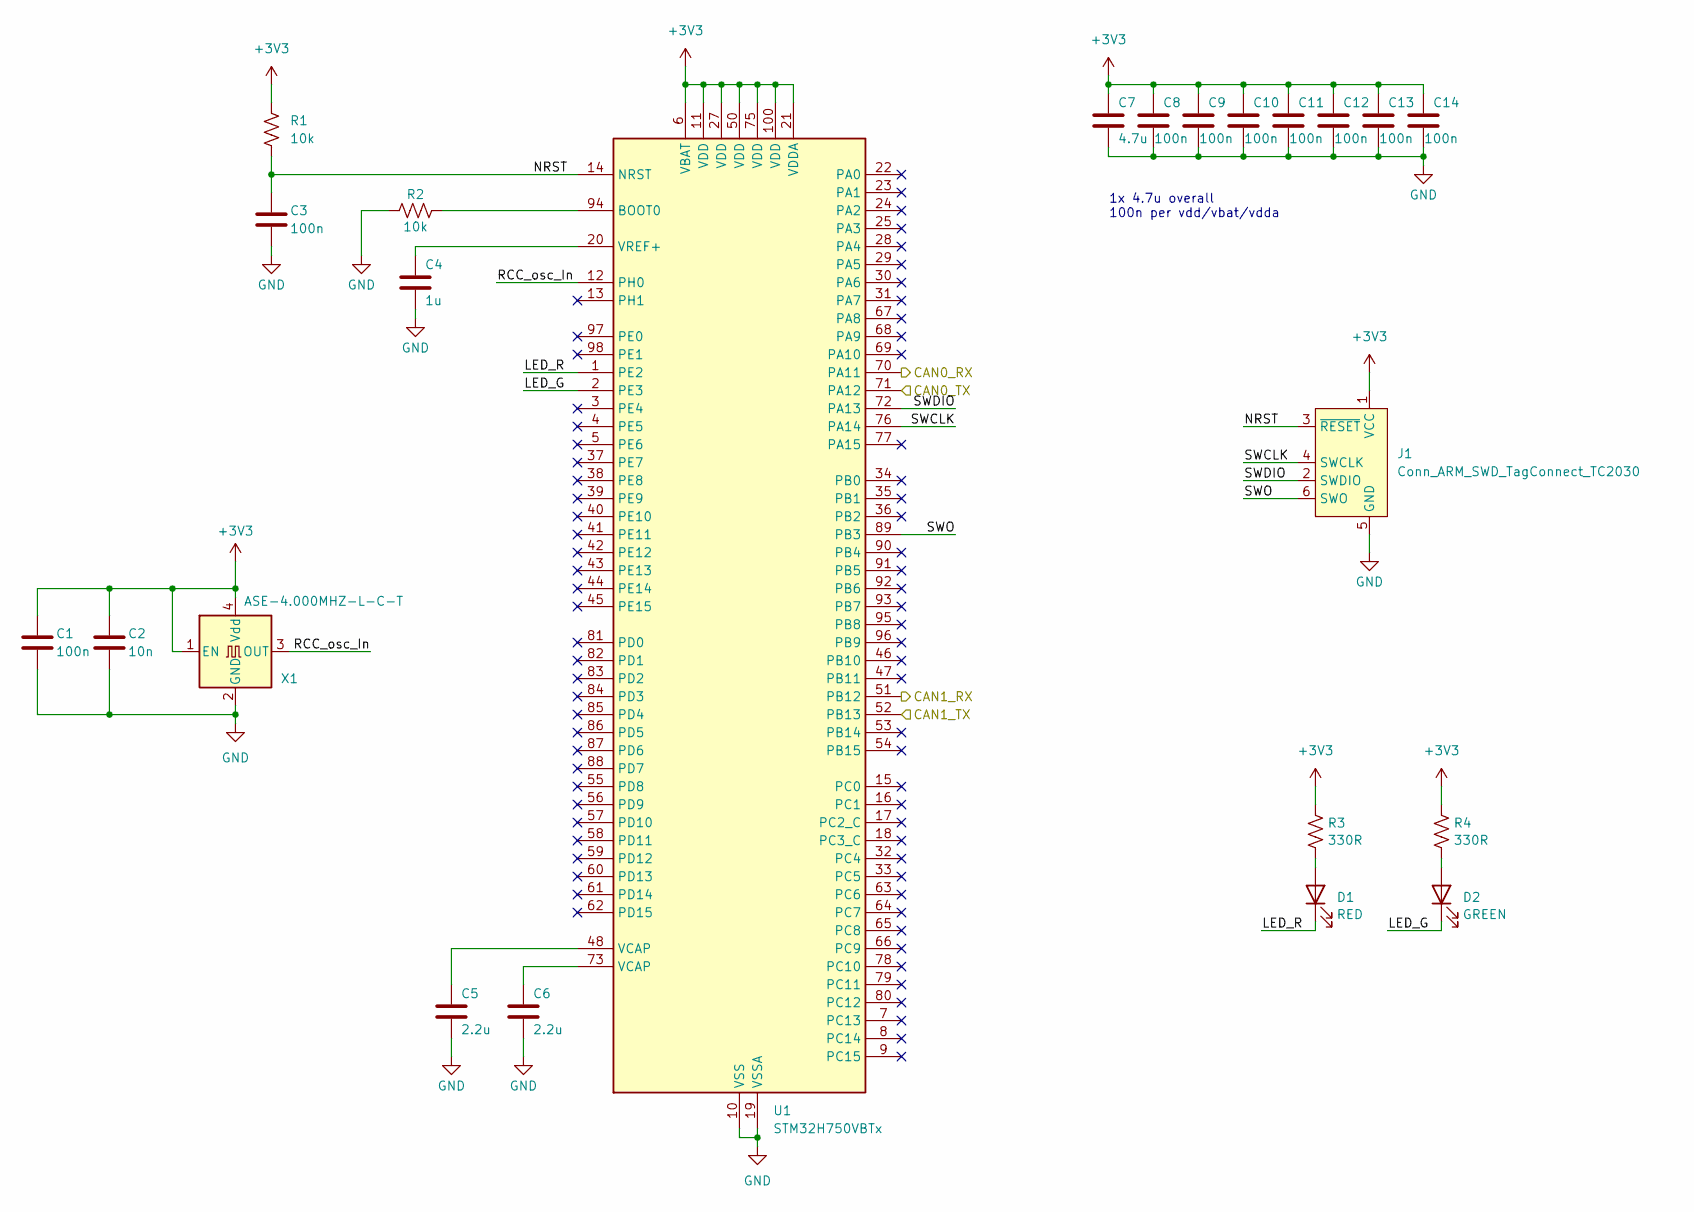
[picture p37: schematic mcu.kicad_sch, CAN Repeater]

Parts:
C1, C3, C8, C9, C10, C11, C12, C13, C14: 100n; C_0603_1608Metric_Pad1.08x0.95mm_HandSolder
C2: 10n; C_0603_1608Metric_Pad1.08x0.95mm_HandSolder
C4: 1u; C_0603_1608Metric_Pad1.08x0.95mm_HandSolder
C5, C6: 2.2u; C_0603_1608Metric_Pad1.08x0.95mm_HandSolder
C7: 4.7u; C_0603_1608Metric_Pad1.08x0.95mm_HandSolder
D1: RED; LED_1206_3216Metric_Pad1.42x1.75mm_HandSolder
D2: GREEN; LED_1206_3216Metric_Pad1.42x1.75mm_HandSolder
J1: Conn_ARM_SWD_TagConnect_TC2030; Tag-Connect_TC2030-IDC-FP_2x03_P1.27mm_Vertical
R1, R2: 10k; R_0603_1608Metric_Pad0.98x0.95mm_HandSolder
R3, R4: 330R; R_0603_1608Metric_Pad0.98x0.95mm_HandSolder
U1: STM32H750VBTx; LQFP-100_14x14mm_P0.5mm
X1: ASE-4.000MHZ-L-C-T; Oscillator_SMD_Abracon_ASE-4Pin_3.2x2.5mm; LCSC Part # C437121

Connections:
+3V3: C1.1, C2.1, C7.1, C8.1, C9.1, C10.1, C11.1, C12.1, C13.1, C14.1, J1.1 (VCC), R1.1, R3.1, R4.1, U1.6 (VBAT), U1.11 (VDD), U1.21 (VDDA), U1.27 (VDD), U1.50 (VDD), U1.75 (VDD), U1.100 (VDD), X1.1 (EN), X1.4 (Vdd); also elsewhere on the board
/CAN/CAN0_RX: U1.70 (PA11); also elsewhere on the board
/CAN/CAN0_TX: U1.71 (PA12); also elsewhere on the board
/CAN/CAN1_RX: U1.51 (PB12); also elsewhere on the board
/CAN/CAN1_TX: U1.52 (PB13); also elsewhere on the board
/MCU/LED_G: D2.1 (K), U1.2 (PE3)
/MCU/LED_R: D1.1 (K), U1.1 (PE2)
/MCU/NRST: C3.1, J1.3 (~RESET), R1.2, U1.14 (NRST)
/MCU/RCC_osc_In: U1.12 (PH0), X1.3 (OUT)
/MCU/SWCLK: J1.4 (SWCLK), U1.76 (PA14)
/MCU/SWDIO: J1.2 (SWDIO), U1.72 (PA13)
/MCU/SWO: J1.6 (SWO), U1.89 (PB3)
GND: C1.2, C2.2, C3.2, C4.2, C5.2, C6.2, C7.2, C8.2, C9.2, C10.2, C11.2, C12.2, C13.2, C14.2, J1.5 (GND), R2.1, U1.10 (VSS), U1.19 (VSSA), U1.26 (VSS), U1.49 (VSS), U1.74 (VSS), U1.99 (VSS), X1.2 (GND); also elsewhere on the board
unnamed: C5.1, U1.48 (VCAP)
unnamed: C6.1, U1.73 (VCAP)
unnamed: D1.2 (A), R3.2
unnamed: D2.2 (A), R4.2
unnamed: R2.2, U1.94 (BOOT0)
unnamed: C4.1, U1.20 (VREF+)

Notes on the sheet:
1x 4.7u overall 100n per vdd/vbat/vdda

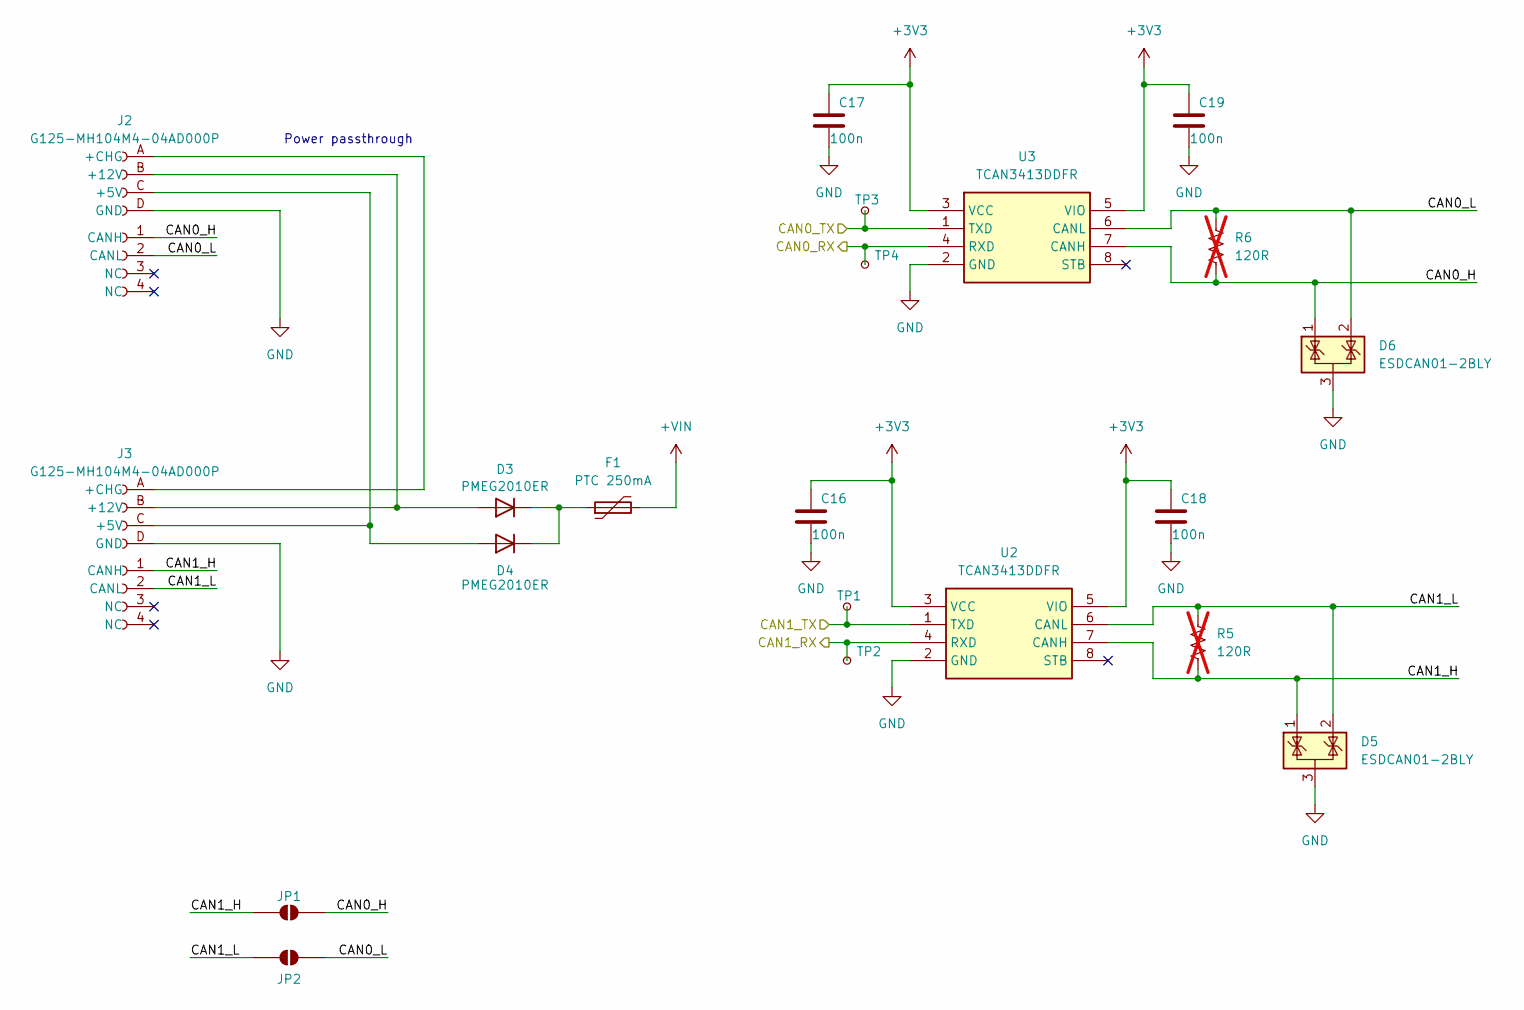
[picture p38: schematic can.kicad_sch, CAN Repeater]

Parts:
C16, C17, C18, C19: 100n; C_0603_1608Metric_Pad1.08x0.95mm_HandSolder
D3, D4: PMEG2010ER; Nexperia_CFP3_SOD-123W
D5, D6: ESDCAN01-2BLY; SOT-23; LCSC Part # C1976606
F1: PTC 250mA; Fuse_1206_3216Metric_Pad1.42x1.75mm_HandSolder
J2, J3: G125-MH104M4-04AD000P; connector_Harwin_G125-MH104M4-04AD000P
JP1, JP2: SolderJumper_2_Open; SolderJumper-2_P1.3mm_Open_RoundedPad1.0x1.5mm
R5, R6: 120R; R_0603_1608Metric_Pad0.98x0.95mm_HandSolder; not fitted
TP1, TP3: RCAN_TX; TestPoint_Pad_D1.0mm
TP2, TP4: RCAN_RX; TestPoint_Pad_D1.0mm
U2, U3: TCAN3413DDFR; Manufacturer_Part_Number TCAN3413DDFR

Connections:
+3V3: C16.1, C17.1, C18.1, C19.1, U2.3 (VCC), U2.5 (VIO), U3.3 (VCC), U3.5 (VIO); also elsewhere on the board
+VIN: F1.2; also elsewhere on the board
/CAN/CAN0_H: D6.1 (K), J2.1 (CANH), JP1.2 (B), R6.2, U3.7 (CANH)
/CAN/CAN0_L: D6.2 (K), J2.2 (CANL), JP2.2 (B), R6.1, U3.6 (CANL)
/CAN/CAN0_RX: TP4.1 (1_1), U3.4 (RXD); also elsewhere on the board
/CAN/CAN0_TX: TP3.1 (1_1), U3.1 (TXD); also elsewhere on the board
/CAN/CAN1_H: D5.1 (K), J3.1 (CANH), JP1.1 (A), R5.2, U2.7 (CANH)
/CAN/CAN1_L: D5.2 (K), J3.2 (CANL), JP2.1 (A), R5.1, U2.6 (CANL)
/CAN/CAN1_RX: TP2.1 (1_1), U2.4 (RXD); also elsewhere on the board
/CAN/CAN1_TX: TP1.1 (1_1), U2.1 (TXD); also elsewhere on the board
GND: C16.2, C17.2, C18.2, C19.2, D5.3 (A), D6.3 (A), J2.D (GND), J3.D (GND), U2.2 (GND), U3.2 (GND); also elsewhere on the board
unnamed: D3.2 (A), J2.B (+12V), J3.B (+12V)
unnamed: D3.1 (K), D4.1 (K), F1.1
unnamed: D4.2 (A), J2.C (+5V), J3.C (+5V)
unnamed: J2.A (+CHG), J3.A (+CHG)

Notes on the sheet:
Power passthrough

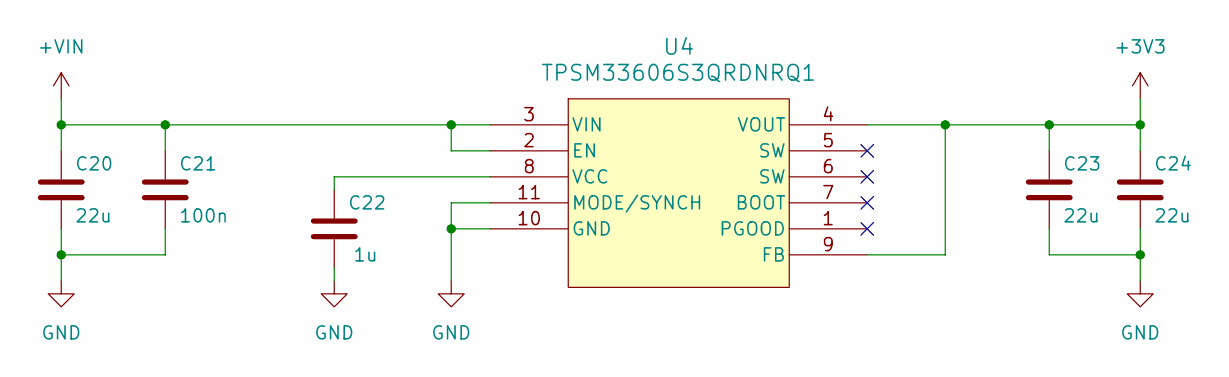
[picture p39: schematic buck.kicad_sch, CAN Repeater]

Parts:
C20, C23, C24: 22u; C_0805_2012Metric_Pad1.18x1.45mm_HandSolder
C21: 100n; C_0603_1608Metric_Pad1.08x0.95mm_HandSolder
C22: 1u; C_0603_1608Metric_Pad1.08x0.95mm_HandSolder
U4: TPSM33606S3QRDNRQ1

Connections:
+3V3: C23.1, C24.1, U4.4 (VOUT), U4.9 (FB); also elsewhere on the board
+VIN: C20.1, C21.1, U4.2 (EN), U4.3 (VIN); also elsewhere on the board
GND: C20.2, C21.2, C22.2, C23.2, C24.2, U4.10 (GND), U4.11 (MODE/SYNCH); also elsewhere on the board
unnamed: C22.1, U4.8 (VCC)

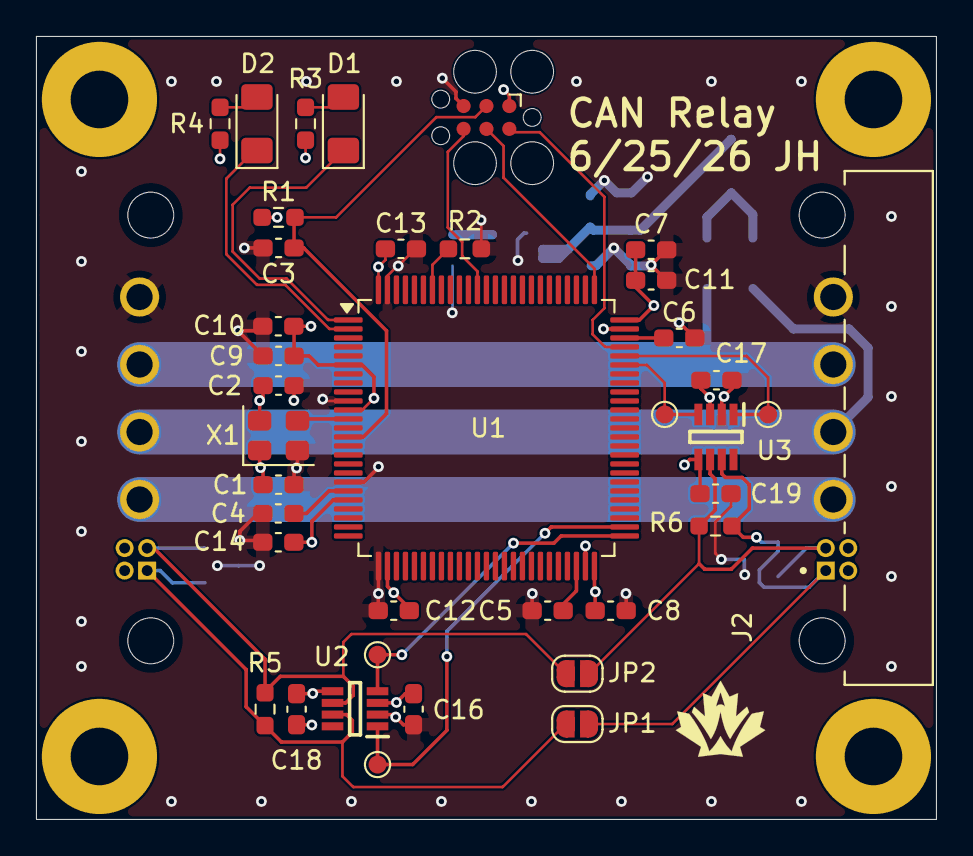
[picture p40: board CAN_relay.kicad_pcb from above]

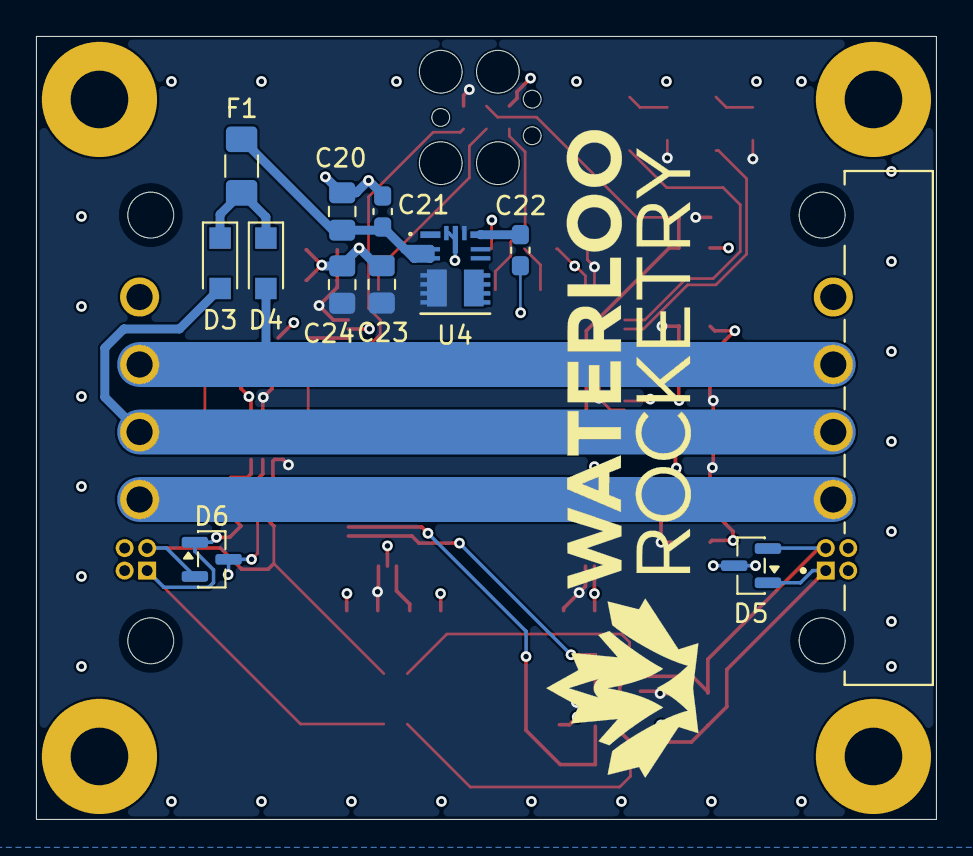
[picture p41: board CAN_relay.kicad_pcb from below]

Board: 4 copper layers, 50.0 x 43.5 mm, 54 parts (12 on the bottom side), 29 nets.

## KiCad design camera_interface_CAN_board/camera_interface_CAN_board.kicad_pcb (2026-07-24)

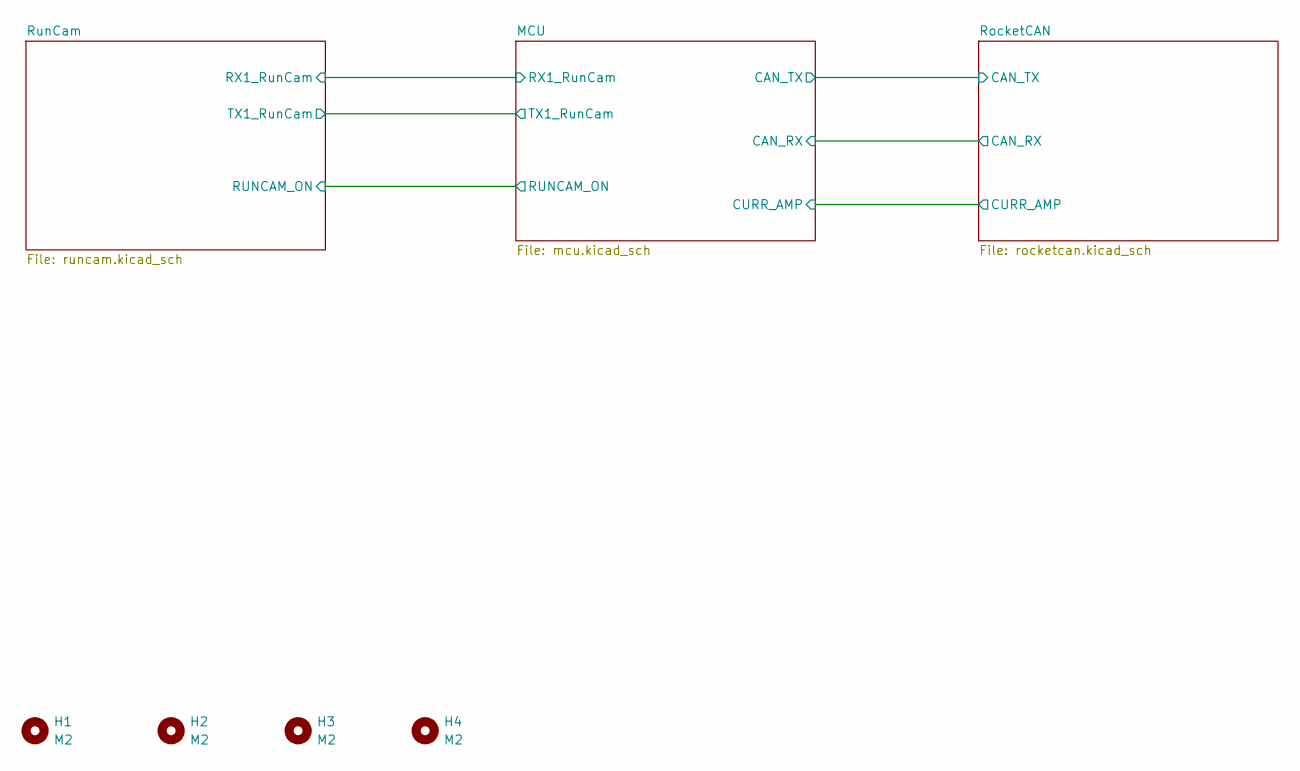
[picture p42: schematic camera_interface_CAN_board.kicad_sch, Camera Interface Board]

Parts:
H1, H2, H3, H4: M2; MountingHole_2.2mm_M2


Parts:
C11: 1uF; C_0603_1608Metric_Pad1.08x0.95mm_HandSolder
C12: 2.2nF; C_0603_1608Metric_Pad1.08x0.95mm_HandSolder
C13, C14: 10uF; C_0805_2012Metric_Pad1.18x1.45mm_HandSolder
J3: Analog_Video; PinSocket_1x02_P1.27mm_Vertical
J4: G125-MG10605M4P; connector_Harwin_G125–MG10605M4P
R9: 10K; R_0603_1608Metric_Pad0.98x0.95mm_HandSolder
R11: 0R; R_0603_1608Metric_Pad0.98x0.95mm_HandSolder
R12: 2k; R_0603_1608Metric_Pad0.98x0.95mm_HandSolder; not fitted
R13: 1k; R_0603_1608Metric_Pad0.98x0.95mm_HandSolder
R14: 2k; R_0603_1608Metric_Pad0.98x0.95mm_HandSolder
U5: TPS22958NDGKR; SOP65P490X110-8N; Manufacturer_Part_Number TPS22958NDGKR

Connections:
+5V: C11.2, R9.1, U5.1 (VIN), U5.3 (VBIAS), U5.4 (VIN); also elsewhere on the board
/MCU/RUNCAM_ON: R9.2, U5.2 (ON); also elsewhere on the board
/MCU/RX1_RunCam: R11.1; also elsewhere on the board
/MCU/TX1_RunCam: R13.1; also elsewhere on the board
/RunCam/RX1_RunCam_3V3: J4.4, R11.2, R12.2
/RunCam/Runcam_5V: C13.2, C14.2, J4.3, U5.5 (VOUT), U5.8 (VOUT)
/RunCam/TX1_RunCam_3V3: J4.5, R13.2, R14.2
/RunCam/Video_Out: J3.1, J4.1
GND: C11.1, C12.1, C13.1, C14.1, J3.2, J4.6, R12.1, R14.1, U5.6 (GND); also elsewhere on the board
unnamed: C12.2, U5.7 (CT)

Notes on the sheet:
To connect runcam analog video out for settings menu


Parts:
C4, C5, C9, C10: 0.1uF; C_0603_1608Metric_Pad1.08x0.95mm_HandSolder
C6: 1uF; C_0603_1608Metric_Pad1.08x0.95mm_HandSolder
C7: 10nF; C_0603_1608Metric_Pad1.08x0.95mm_HandSolder; not fitted
C8: 10uF; C_0805_2012Metric_Pad1.18x1.45mm_HandSolder
C15: 2.2nF; C_0603_1608Metric_Pad1.08x0.95mm_HandSolder
D4: SMF13CA; D_SMF
J2: G125-MH104M4-04AD000P; connector_Harwin_G125-MH104M4-04AD000P
R5: 390k; R_0603_1608Metric_Pad0.98x0.95mm_HandSolder
R6: 3.3k; R_0603_1608Metric_Pad0.98x0.95mm_HandSolder
R7: 40mR; R_0805_2012Metric_Pad1.20x1.40mm_HandSolder
R8: 330R; R_0603_1608Metric_Pad0.98x0.95mm_HandSolder
R10: 120R; R_0603_1608Metric_Pad0.98x0.95mm_HandSolder; not fitted
TP1: 5V; TestPoint_Pad_D1.0mm
U2: canhw:MCP2562; SOIC-8_3.9x4.9mm_P1.27mm
U3: TPS259472ARPW; TPS25947xx
U4: INA180A3; SOT-23-5_HandSoldering

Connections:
+5V: C4.1, C5.1, C9.2, R7.1, TP1.1 (1_1), U2.3 (VDD), U2.5 (VIO), U4.4 (-), U4.5 (V+); also elsewhere on the board
/MCU/CAN_RX: U2.4 (RXD); also elsewhere on the board
/MCU/CAN_TX: U2.1 (TXD); also elsewhere on the board
/MCU/CURR_AMP: C10.2, R8.1; also elsewhere on the board
/RocketCAN/5V_IN: C6.2, D4.2 (A2), J2.C (+5V), R5.1, U3.5 (IN)
/RocketCAN/CANH: J2.1 (CANH), R10.2, U2.7 (CANH)
/RocketCAN/CANL: J2.2 (CANL), R10.1, U2.6 (CANL)
GND: C4.2, C5.2, C6.1, C7.1, C8.1, C9.1, C10.1, C15.1, D4.1 (A1), J2.D (GND), R6.2, U2.2 (VSS), U2.8 (STBY), U3.8 (GND), U4.2 (GND); also elsewhere on the board
unnamed: R8.2, U4.1
unnamed: C15.2, U3.7 (DVDT)
unnamed: R5.2, U3.1 (EN/UVLO)
unnamed: R6.1, U3.9 (ILM)
unnamed: C7.2, U3.10 (ITIMER)
unnamed: C8.2, R7.2, U3.6 (OUT), U4.3 (+)

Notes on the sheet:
13Vrwm to survive accidental 12V input
Auto-retry version. Latch-off also available
5.7V OVC
Datasheet: for supply voltages greater than 5V or systems which can be exposed to reverse polarity on input supply, it is recommended to use a pull-up resistor with a minimum value of 350kΩ.
1A limit
1A * Rsense * 100V/V = 4.096V R=0.041R, choose R=0.04


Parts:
C1, C2: 27pF; C_0603_1608Metric_Pad1.08x0.95mm_HandSolder
C3: 0.1uF; C_0603_1608Metric_Pad1.08x0.95mm_HandSolder
C16: 1uF; C_0603_1608Metric_Pad1.08x0.95mm_HandSolder
D1: WHITE; LED_1206_3216Metric
D2: RED; LED_1206_3216Metric
D3: BLUE; LED_1206_3216Metric
J1: Programming Header; PinSocket_5x2.54_SMD_90deg_952-3198-1-ND
R1, R2, R3: 330R; R_0603_1608Metric_Pad0.98x0.95mm_HandSolder
R4: 10K; R_0603_1608Metric_Pad0.98x0.95mm_HandSolder
U1: canhw:PIC18F26K83; SOIC-28W_7.5x18.7mm_P1.27mm
Y1: ABM8G-12.000MHZ-18-D2Y-T; Crystal_SMD_Abracon_ABM8G-4Pin_3.2x2.5mm

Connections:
+5V: C3.2, C16.2, D1.2 (A), D2.2 (A), D3.2 (A), J1.2, R4.1, U1.20 (VDD); also elsewhere on the board
/MCU/B_LED: R3.2, U1.4 (RA2)
/MCU/CAN_RX: U1.16 (RC5); also elsewhere on the board
/MCU/CAN_TX: U1.15 (RC4); also elsewhere on the board
/MCU/CURR_AMP: U1.26 (RB5); also elsewhere on the board
/MCU/ICSPCLK: J1.5, U1.27 (RB6/ICSPCLK)
/MCU/ICSPDAT: J1.4, U1.28 (RB7/ICSPDAT)
/MCU/OSC1: C1.1, U1.9 (RA7/OSC1), Y1.1
/MCU/OSC2: C2.2, U1.10 (RA6/OSC2), Y1.3
/MCU/RUNCAM_ON: U1.5 (RA3); also elsewhere on the board
/MCU/RX1_RunCam: U1.13 (RC2); also elsewhere on the board
/MCU/R_LED: R2.2, U1.3 (RA1)
/MCU/TX1_RunCam: U1.14 (RC3); also elsewhere on the board
/MCU/W_LED: R1.2, U1.2 (RA0)
/MCU/~MCLR: J1.1, R4.2, U1.1 (~MCLR)
GND: C1.2, C2.1, C3.1, C16.1, J1.3, U1.8 (VSS), U1.19 (VSS), Y1.2, Y1.4; also elsewhere on the board
unnamed: D1.1 (K), R1.1
unnamed: D2.1 (K), R2.1
unnamed: D3.1 (K), R3.1

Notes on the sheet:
12 MHz crystal oscillator
CL = 18pF from data sheet, Cstray = 5pF CL = (C1xC2)/(c1+c2)+Cstray C1 = c2 18=C /2+5 c =26pF C = 22pF from E12 



Board: 4 copper layers, 38.6 x 29.0 mm, 49 parts (27 on the bottom side), 33 nets.

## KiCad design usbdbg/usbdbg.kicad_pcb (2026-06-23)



Board: 2 copper layers, 23.3 x 52.3 mm, 35 parts (8 on the bottom side), 31 nets.

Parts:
C1, C2, C3: 0.1u; C_0603_1608Metric_Pad1.08x0.95mm_HandSolder
C4: 10u; C_0603_1608Metric_Pad1.08x0.95mm_HandSolder
C6: 1uF; C_0603_1608Metric_Pad1.08x0.95mm_HandSolder
C7, C15: 10nF; C_0603_1608Metric_Pad1.08x0.95mm_HandSolder
C8: 10uF; C_0805_2012Metric_Pad1.18x1.45mm_HandSolder
D1: GREEN; LED_1206_3216Metric_Pad1.42x1.75mm_HandSolder
D2: RED; LED_1206_3216Metric_Pad1.42x1.75mm_HandSolder
F1: 1A; Fuse_1206_3216Metric
H1, H2: MountingHole_Pad; MountingHole_3.2mm_M3_Pad_Via
J1: Programming Header; PinSocket_5x2.54_SMD_90deg_952-3198-1-ND
J3: BUS CONN; CONN_SD-43045-001_04_MOL
J4: USB_C_Receptacle_USB2.0_14P; 2171790001_MOL
JP1, JP2: Jumper; PinHeader_1x02_P2.54mm_Vertical
R1, R2: 330R; R_0603_1608Metric_Pad0.98x0.95mm_HandSolder
R3, R4: 10k; R_0603_1608Metric_Pad0.98x0.95mm_HandSolder
R5: 120R; R_0603_1608Metric_Pad0.98x0.95mm_HandSolder
R6, R7: 5.1k; C_0603_1608Metric_Pad1.08x0.95mm_HandSolder
R9: 6.65k; R_0603_1608Metric_Pad0.98x0.95mm_HandSolder
TP1, TP2, TP3, TP4: TestPoint; KEYSTONE_5116
U1: PIC16F1455; SOIC-14_3.9x8.7mm_P1.27mm
U2: MCP2515; SOIC-18W_7.5x11.6mm_P1.27mm
U3: MCP2562; SOIC-8_3.9x4.9mm_P1.27mm
U4: TPS259472ARPW; TPS25947xx
U5: USBLC6-2SC6; SOT-23-6

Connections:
+5V: C1.1, C3.1, C4.1, C8.2, J1.2, JP2.1 (A), R1.2, R2.1, R3.1, R4.1, TP3.1 (1_1), U1.1 (VDD), U2.17 (~RESET), U2.18 (VDD), U3.3 (VDD), U3.5 (VIO), U4.6 (OUT)
/CANH: J3.3, R5.2, TP1.1 (1_1), U3.7 (CANH)
/CANL: J3.4, JP1.2 (B), TP2.1 (1_1), U3.6 (CANL)
/CAN_INT: R4.2, U1.2 (RA5), U2.12 (~INT)
/CLKOUT: U1.3 (RA4), U2.8 (OSC1)
/CS: U1.7 (RC3), U2.16 (~CS)
/ICSPCLK: J1.5, U1.9 (RC1/ICSPCLK), U2.15 (SO)
/ICSPDAT: J1.4, U1.10 (RC0/ICSPDAT), U2.13 (SCK)
/MOSI: U1.8 (RC2), U2.14 (SI)
/USB_D+: U1.13 (RA0/D+), U5.4 (I/O2)
/USB_D-: U1.12 (RA1/D-), U5.6 (I/O1)
/~MCLR: J1.1, R3.2, U1.4 (RA3/~MCLR)
GND: C1.2, C2.2, C3.2, C4.2, C6.1, C7.1, C8.1, C15.1, H1.1 (1_1), H2.1 (1_1), J1.3, J3.2, J4.A1 (GND), J4.A12 (GND), R6.2, R7.2, R9.2, TP4.1 (1_1), U1.14 (VSS), U2.9 (VSS), U3.2 (VSS), U3.8 (STBY), U4.8 (GND), U5.2 (GND)
unnamed: D1.2 (A), R1.1
unnamed: D1.1 (K), U1.6 (RC4)
unnamed: D2.2 (A), R2.2
unnamed: D2.1 (K), U1.5 (RC5)
unnamed: F1.2, J4.A4 (VBUS), J4.A9 (VBUS)
unnamed: J3.1, JP2.2 (B)
unnamed: J4.A5 (CC1), R7.1
unnamed: J4.B5 (CC2), R6.1
unnamed: J4.A6 (D+), J4.B6 (D+), U5.3 (I/O2)
unnamed: J4.A7 (D-), J4.B7 (D-), U5.1 (I/O1)
unnamed: JP1.1 (A), R5.1
unnamed: C2.1, U1.11 (VUSB3V3)
unnamed: U2.2 (RXCAN), U3.4 (RXD)
unnamed: U2.1 (TXCAN), U3.1 (TXD)
unnamed: C15.2, U4.7 (DVDT)
unnamed: C6.2, F1.1, U4.1 (EN/UVLO), U4.5 (IN), U5.5 (VBUS)
unnamed: R9.1, U4.9 (ILM)
unnamed: C7.2, U4.10 (ITIMER)

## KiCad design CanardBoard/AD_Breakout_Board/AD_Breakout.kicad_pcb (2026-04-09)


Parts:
C18, C21: 10uF; C_0805_2012Metric
C19, C20, C22, C23, C24: 0.1uF; C_0402_1005Metric
L1: 2.2uH; L_1008_2520Metric; MPN LQM2HPN2R2MG0L
R8: 0.22R; R_0603_1608Metric
U4: REF2041; Mouser Part Number 595-REF2041AIDDCR

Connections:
+2.048V_REF: C24.1, U4.1 (VBIAS); also elsewhere on the board
+4.096V_REF: C23.1, U4.5 (VREF); also elsewhere on the board
+5V: C18.1, C19.1, L1.1; also elsewhere on the board
+5VA: C20.1, C21.1, C22.1, R8.2, U4.3 (EN), U4.4 (VIN); also elsewhere on the board
GND: C18.2, C19.2, C20.2, C21.2, C22.2, C23.2, C24.2, U4.2 (GND); also elsewhere on the board
unnamed: L1.2, R8.1


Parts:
C14, C15, C16: 0.1uF; C_0402_1005Metric
R6, R7: 1k; R_0402_1005Metric
R9: 10k; R_0402_1005Metric
U3: ADS1219IRTER; Manufacturer_Part_Number ADS1219IRTER

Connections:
+2.048V_REF: C14.1, U3.4 (AIN3), U3.7 (REFP), U3.9 (AIN0); also elsewhere on the board
+3V3: C16.1, R6.1, R7.1, R9.1, U3.11 (DVDD); also elsewhere on the board
+5VA: C15.1, U3.10 (AVDD); also elsewhere on the board
/ADC/ADC_ALERT: U3.12 (~DRDY); also elsewhere on the board
/ADC/ADI_SCL: R6.2, U3.14 (SCL); also elsewhere on the board
/ADC/ADI_SDA: R7.2, U3.13 (SDA); also elsewhere on the board
/ADC/GYRO_OUT: U3.8 (AIN1); also elsewhere on the board
/ADC/TEMP_OUT: U3.5 (AIN2); also elsewhere on the board
GND: C14.2, C15.2, C16.2, U3.2 (DGND), U3.3 (AGND), U3.6 (REFN), U3.15 (A0), U3.16 (A1), U3.17 (EP); also elsewhere on the board
unnamed: R9.2, U3.1 (~RESET)

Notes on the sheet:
I2C Fast Mode Plus
Gyro uses left-handed coordinate system inverting in hardware to match board


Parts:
C17: 10uF; C_0805_2012Metric
H1, H2, H3: M2; MountingHole_2.2mm_M2_Pad
J1: 1373827; Mouser Part Number 651-1373827

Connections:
+3V3: C17.1, J1.A3, J1.B4; also elsewhere on the board
+5V: J1.A2, J1.B5; also elsewhere on the board
/ADC/ADC_ALERT: J1.A6; also elsewhere on the board
/ADC/ADI_SCL: J1.A4; also elsewhere on the board
/ADC/ADI_SDA: J1.A5; also elsewhere on the board
/Accelerometer/ACCEL_INT: J1.B3; also elsewhere on the board
/ST1: J1.B2; also elsewhere on the board
/ST2: J1.B1; also elsewhere on the board
GND: C17.2, J1.A1, J1.B6, J1.MP1, J1.MP2, J1.MP3, J1.MP4; also elsewhere on the board


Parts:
C1, C5, C7, C8: 0.1uF; C_0402_1005Metric
C2, C3, C9: 22nF; C_0402_1005Metric
C4: 2.2nF; C_0402_1005Metric
C6: 6.8nF; C_0402_1005Metric
R1: 120k; R_0402_1005Metric; not fitted
R2, R4: 3.3k; R_0402_1005Metric
R3, R5: 10k; R_0402_1005Metric
U1: ADXRS649BBGZ; Mouser Part Number N/A

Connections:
+4.096V_REF: C8.1, U1.E1 (VRATIO_1), U1.E2 (VRATIO_2); also elsewhere on the board
+5V: C1.1, U1.E6 (VDD_1), U1.E7 (VDD_2); also elsewhere on the board
+5VA: C5.1, U1.A3 (AVCC_1), U1.B3 (AVCC_2); also elsewhere on the board
/ADC/GYRO_OUT: C9.1, R4.2; also elsewhere on the board
/ADC/TEMP_OUT: C7.1, R2.2; also elsewhere on the board
/Gyroscope/TEMP: R2.1, U1.F3 (TEMP_1), U1.G3 (TEMP_2)
/ST1: R5.2, U1.F5 (ST1_1), U1.G5 (ST1_2); also elsewhere on the board
/ST2: R3.2, U1.F4 (ST2_1), U1.G4 (ST2_2); also elsewhere on the board
GND: C1.2, C4.2, C5.2, C7.2, C8.2, C9.2, R3.1, R5.1, U1.F1 (AGND_1), U1.F7 (PGND_1), U1.G2 (AGND_2), U1.G6 (PGND_2); also elsewhere on the board
unnamed: C2.1, U1.A5 (CP1_1), U1.B5 (CP1_2)
unnamed: C2.2, U1.A4 (CP2_1), U1.B4 (CP2_2)
unnamed: C3.1, U1.C6 (CP3_1), U1.C7 (CP3_2)
unnamed: C3.2, U1.A6 (CP4_1), U1.B7 (CP4_2)
unnamed: C4.1, U1.D6 (CP5_1), U1.D7 (CP5_2)
unnamed: C6.1, R1.2, R4.1, U1.A2 (RATEOUT_1), U1.B1 (RATEOUT_2)
unnamed: C6.2, R1.1, U1.C1 (SUMJ_1), U1.C2 (SUMJ_2)

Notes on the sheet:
-3dB frequency = ~130Hz
Datasheet recommended values (2.2kHz)
Adj max rate to 50k dps


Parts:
C10: 1uF; C_0402_1005Metric
C11, C12, C13: 0.1uF; C_0402_1005Metric
U2: ADXL380; Mouser Part Number 584-ADXL380-1BCCZRL7

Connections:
+3V3: C10.1, C11.1, C12.1, U2.10 (VS), U2.11 (VDDIO); also elsewhere on the board
/ADC/ADI_SCL: U2.2 (SCLK/SCL); also elsewhere on the board
/ADC/ADI_SDA: U2.3 (SDI/SDA); also elsewhere on the board
/Accelerometer/ACCEL_INT: U2.6 (INT0); also elsewhere on the board
GND: C10.2, C11.2, C12.2, C13.2, U2.4 (SDO/ASEL0), U2.5 (~CS/ASEL1), U2.9 (GND); also elsewhere on the board
unnamed: C13.1, U2.8 (V1P8)



Board: 4 copper layers, 20.0 x 20.0 mm, 42 parts (6 on the bottom side), 25 nets.

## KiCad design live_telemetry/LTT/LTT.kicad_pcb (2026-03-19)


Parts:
C5, C10, C35: 0.1uF; C_0402_1005Metric_Pad0.74x0.62mm_HandSolder
C6: 1.5nF; C_0402_1005Metric_Pad0.74x0.62mm_HandSolder
C7, C29, C34: 39pF; C_0402_1005Metric_Pad0.74x0.62mm_HandSolder
C8: 12pF; C_0402_1005Metric_Pad0.74x0.62mm_HandSolder; not fitted
C9, C12, C14, C15, C16, C19, C23, C26, C28, C30, C33: 47nF; C_0402_1005Metric_Pad0.74x0.62mm_HandSolder
C11, C49: 100pF; C_0402_1005Metric_Pad0.74x0.62mm_HandSolder
C13, C17, C18: 20pF; C_0402_1005Metric_Pad0.74x0.62mm_HandSolder
C20: 6.2pF; C_0402_1005Metric_Pad0.74x0.62mm_HandSolder
C21, C50: 10nF; C_0402_1005Metric_Pad0.74x0.62mm_HandSolder
C22, C25: 20pF; C_0402_1005Metric_Pad0.74x0.62mm_HandSolder; not fitted
C24: 220nF; C_0402_1005Metric_Pad0.74x0.62mm_HandSolder
C27, C51: 33pF; C_0402_1005Metric_Pad0.74x0.62mm_HandSolder
C31, C32: 3.3pF; C_0402_1005Metric_Pad0.74x0.62mm_HandSolder
C39, C40: 15pF; C_0402_1005Metric_Pad0.74x0.62mm_HandSolder
J2, J3: Conn_Coaxial; SMA_Samtec_SMA-J-P-H-ST-EM1_EdgeMount
L1: 24nH; L_0402_1005Metric_Pad0.77x0.64mm_HandSolder
L2: 8.2nH; L_0402_1005Metric_Pad0.77x0.64mm_HandSolder
L3, L4: 1nH; L_0402_1005Metric_Pad0.77x0.64mm_HandSolder
L5: 15nH; L_0402_1005Metric_Pad0.77x0.64mm_HandSolder
L6, L7, L8: 12nH; L_0402_1005Metric_Pad0.77x0.64mm_HandSolder
L11: 33nH; L_0402_1005Metric_Pad0.77x0.64mm_HandSolder
R5, R9: 0R; R_0402_1005Metric_Pad0.72x0.64mm_HandSolder
R6: 6.8K; R_0402_1005Metric_Pad0.72x0.64mm_HandSolder
R7: 56K; R_0402_1005Metric_Pad0.72x0.64mm_HandSolder
R8: 3.3K; R_0402_1005Metric_Pad0.72x0.64mm_HandSolder
R10: 100R; R_0603_1608Metric_Pad0.98x0.95mm_HandSolder
R15: 10; R_0402_1005Metric_Pad0.72x0.64mm_HandSolder
TP7: RX; U.FL_Molex_MCRF_73412-0110_Vertical
TP8: TX; U.FL_Molex_MCRF_73412-0110_Vertical
U3: GRF5509; QFN50P300X300X85-17N
U4: CC1200; QFN-32-1EP_5x5mm_P0.5mm_EP3.45x3.45mm
U5, U11: MASWSS0204TR-3000; SOT-363_1P25X2_MCM
U6: NC7WZU04P6X; SOT-363_SC-70-6_Handsoldering
U10: PD0810J5050S2HF; Manufacturer_Part_Number PD0810J5050S2HF
Y2: 40MHz; Crystal_SMD_3225-4Pin_3.2x2.5mm

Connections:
+3V3: C9.1, C12.1, C15.1, C19.1, C23.1, C26.1, C28.1, C30.1, C33.1, C35.1, C49.1, C50.1, C51.1, R15.1, U4.1 (VDD_GUARD), U4.5 (DVDD), U4.12 (DVDD), U4.13 (AVDD_IF), U4.15 (AVDD_RF), U4.22 (AVDD_SYNTH1), U4.25 (AVDD_PFD_CHP), U4.27 (AVDD_SYNTH2), U4.28 (AVDD_XOSC), U6.5 (VCC); also elsewhere on the board
+5V: C10.1, C11.1, L1.1, L3.1, R6.1, R8.1, U3.12 (BIAS); also elsewhere on the board
/MCU/CS: U4.11 (~CS); also elsewhere on the board
/MCU/DIS1: R8.2, U3.1 (V_{EN1}); also elsewhere on the board
/MCU/DIS2: R6.2, U3.16 (V_{EN2}); also elsewhere on the board
/MCU/GPIO2: U4.4 (GPIO2); also elsewhere on the board
/MCU/MISO: U4.9 (SO(GPIO1)); also elsewhere on the board
/MCU/MOSI: U4.7 (SI); also elsewhere on the board
/MCU/RESET: U4.2 (~RESET); also elsewhere on the board
/MCU/SCLK: U4.8 (SCLK); also elsewhere on the board
/RF/EXT-PA: C20.2, U3.3 (RF_IN), U3.4 (RF_IN)
/RF/LNA+: C31.1, L5.1, L6.1, U4.19 (LNA_P)
/RF/LNA-: C32.1, L5.2, L7.1, U4.20 (LNA_N)
/RF/RX: C34.2, U5.4 (RF1)
/RF/SW1: U4.10 (GPIO0), U5.3 (V1), U6.1
/RF/SW2: U4.3 (GPIO3), U6.3, U11.1 (V2)
/RF/TRX-PA: L4.1, U4.17 (PA)
/RF/TX: C13.2, U5.6 (RF2)
/RF/XOSC_Q1: C40.1, U4.30 (XOSC_Q1), Y2.1
/RF/XOSC_Q2: C39.1, U4.31 (XOSC_Q2), Y2.3
GND: C5.2, C8.2, C9.2, C10.2, C11.2, C12.2, C14.2, C15.2, C16.2, C18.2, C19.2, C21.2, C22.2, C23.2, C24.2, C25.2, C26.2, C28.2, C30.2, C32.2, C33.2, C35.2, C39.2, C40.2, C49.2, C50.2, J2.2 (Ext), J3.2 (Ext), L2.2, L6.2, R5.1, R7.1, TP7.2 (Ext), TP8.2 (Ext), U3.2 (GND/NC), U3.5 (GND/NC), U3.6 (GND/NC), U3.7 (GND/NC), U3.8 (GND/NC), U3.11 (GND/NC), U3.14 (GND/NC), U3.15 (GND/NC), U4.33 (GND_EP), U5.5 (GND), U6.2 (GND), U10.1 (GND_1), U10.3 (GND_2), U10.5 (GND_3), U11.5 (GND), Y2.2, Y2.4; also elsewhere on the board
unnamed: C5.1, L3.2, R9.2
unnamed: C8.1, C13.1, C17.1, C18.1, C22.1, C25.1, L1.2, U3.9 (RF_OUT/V_{CC2}), U3.10 (RF_OUT/V_{CC2})
unnamed: C20.1, C27.1, L2.1
unnamed: C27.2, L4.2, L11.2
unnamed: C31.2, L7.2, L8.1
unnamed: C7.1, C34.1, L8.2
unnamed: C51.2, L11.1, R15.2
unnamed: J2.1 (In), R10.2, U10.4 (OUTPUT_1), U11.4 (RF1)
unnamed: J3.1 (In), R10.1, U10.6 (OUTPUT_2), U11.6 (RF2)
unnamed: C7.2, TP7.1 (In)
unnamed: C17.2, TP8.1 (In)
unnamed: R9.1, U3.13 (V_{CC1})
unnamed: C24.1, U4.6 (DCPL)
unnamed: C16.1, U4.26 (DCPL_PFD_CHP)
unnamed: C21.1, U4.21 (DCPL_VCO)
unnamed: C14.1, U4.29 (DCPL_XOSC)
unnamed: R5.2, U4.32 (EXT_XOSC)
unnamed: C6.1, U4.23 (LPF0)
unnamed: C6.2, U4.24 (LPF1)
unnamed: R7.2, U4.14 (RBIAS)
unnamed: C29.1, U5.2 (RFC)
unnamed: U5.1 (V2), U6.6
unnamed: U6.4, U11.3 (V1)
unnamed: C29.2, U10.2 (INPUT), U11.2 (RFC)

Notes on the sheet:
Transciever
Load Caps: Datasheet: 10pF Reference Schematic: 15pF
Power Amplifier
RF Switch
CC1200RHBR using XTAL Reference: CC1200EM 868- to 930-MHz http://www.ti.com/lit/zip/swrr121
Power split: solder U10 and R10 Ant switch: solder U11 onto U10 footprint connect pin 1,2 to control pads, cut gnd remove R10
35 + 35j Ohm
Crystal
60 + 60j Ohm to 50 Ohm Balun
Transmitter
See live_telemetry/Waterloo GRF5509 Layout Review #1.pdf Note error on page 2 shorts 3V3 to GND; remedied with C27
Reciever
For tuning


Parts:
C41: 0.1uF; C_0603_1608Metric_Pad1.08x0.95mm_HandSolder
C42: 10uF; C_0603_1608Metric_Pad1.08x0.95mm_HandSolder
C43: 100nF; C_0603_1608Metric_Pad1.08x0.95mm_HandSolder
C44, C45: 22uF; C_0603_1608Metric_Pad1.08x0.95mm_HandSolder
C46: 1 uF; C_0603_1608Metric_Pad1.08x0.95mm_HandSolder
C47: 10 nF; C_0603_1608Metric_Pad1.08x0.95mm_HandSolder
C48: 2.2 uF; C_0603_1608Metric_Pad1.08x0.95mm_HandSolder
F1: Polyfuse 1A; Fuse_1206_3216Metric_Pad1.42x1.75mm_HandSolder
H1, H2, H3, H4: MountingHole_Pad; MountingHole_3.2mm_M3_Pad_Via
J4: G125-MH104M4-04AD000P; connector_Harwin_G125-MH104M4-04AD000P
L10: 4.7uH; L_Bourns-SRN8040_8x8.15mm
R12: 16mR; R_1206_3216Metric_Pad1.30x1.75mm_HandSolder
R13: 56.2K; R_0603_1608Metric_Pad0.98x0.95mm_HandSolder
R14: 10K; R_0603_1608Metric_Pad0.98x0.95mm_HandSolder
TP1: TP_5V; TestPoint_Pad_D3.0mm
TP2: TP_3V3; TestPoint_Pad_D3.0mm
U7: INA180; SOT-23-5_HandSoldering
U8: TPS562200; SOT-23-6
U9: SPX3819M5-L-3-3; SOT-23-5

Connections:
+3V3: C41.1, C48.1, TP2.1, U7.5 (VS), U9.5 (OUT); also elsewhere on the board
+5V: C44.1, C45.1, C46.1, L10.2, R13.1, TP1.1, U9.1 (IN), U9.3 (EN); also elsewhere on the board
+12V: C42.1, R12.1, U7.4 (IN-), U8.3 (VIN), U8.5 (EN)
/MCU/CURR_AMP_CAN: U7.1 (VO); also elsewhere on the board
CANH: J4.1 (CANH); also elsewhere on the board
CANL: J4.2 (CANL); also elsewhere on the board
GND: C41.2, C42.2, C44.2, C45.2, C46.2, C47.2, C48.2, H1.1, H2.1, H3.1, H4.1, J4.D (GND), R14.2, U7.2 (GND), U8.1 (GND), U9.2 (GND); also elsewhere on the board
unnamed: F1.2, J4.C (+5V)
unnamed: F1.1, R12.2, U7.3 (IN+)
unnamed: C43.1, L10.1, U8.2 (SW)
unnamed: C43.2, U8.6 (VBST)
unnamed: R13.2, R14.1, U8.4 (VFB)
unnamed: C47.1, U9.4 (BP)

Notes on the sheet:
100V/V
RocketCAN + Current Sensing
= 3.3V / (100V/V * 2A) = 0.0165R
5V to 3V3 LDO
12V to 5V stepdown


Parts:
C1: 10 uF; C_0603_1608Metric_Pad1.08x0.95mm_HandSolder
C2: 0.1 uF; C_0603_1608Metric_Pad1.08x0.95mm_HandSolder
C3, C4: 27 pF; C_0603_1608Metric_Pad1.08x0.95mm_HandSolder
D1: LED_GREEN; LED_1206_3216Metric_Pad1.42x1.75mm_HandSolder
D2: LED_BLUE; LED_1206_3216Metric_Pad1.42x1.75mm_HandSolder
D3: LED_RED; LED_1206_3216Metric_Pad1.42x1.75mm_HandSolder
J1: Programming Header; PinSocket_5x2.54_SMD_90deg_952-3198-1-ND
R1: 10K; R_0603_1608Metric_Pad0.98x0.95mm_HandSolder
R2, R3, R4: 330R; R_0603_1608Metric_Pad0.98x0.95mm_HandSolder
R11, R16: 0R; R_0402_1005Metric_Pad0.72x0.64mm_HandSolder
TP3: CS; TestPoint_Pad_D1.0mm
TP4: SCLK; TestPoint_Pad_D1.0mm
TP5: MISO; TestPoint_Pad_D1.0mm
TP6: MOSI; TestPoint_Pad_D1.0mm
U1: MCP2562; SOIC-8_3.9x4.9mm_P1.27mm
U2: PIC18F26K83; SOIC-28W_7.5x17.9mm_P1.27mm
Y1: Crystal; Crystal_HC49-4H_Vertical

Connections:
+3V3: C2.2, J1.4, R1.1, R2.2, R3.2, R4.2, U1.5 (VIO), U2.20 (VDD); also elsewhere on the board
+5V: C1.1, U1.3 (VDD); also elsewhere on the board
/MCU/CAN_RX: U1.4 (RXD), U2.11 (RC0)
/MCU/CAN_TX: U1.1 (TXD), U2.12 (RC1)
/MCU/CS: TP3.1, U2.7 (RA5); also elsewhere on the board
/MCU/CURR_AMP_CAN: U2.2 (RA0); also elsewhere on the board
/MCU/DIS1: R16.1; also elsewhere on the board
/MCU/DIS2: R11.2; also elsewhere on the board
/MCU/GPIO2: U2.24 (RB3); also elsewhere on the board
/MCU/ICSPCLK: J1.1, U2.27 (RB6/ICSPCLK)
/MCU/ICSPDAT: J1.2, U2.28 (RB7/ICSPDAT)
/MCU/LED_BLUE: D2.1 (K), U2.5 (RA3)
/MCU/LED_GREEN: D1.1 (K), U2.4 (RA2)
/MCU/LED_RED: D3.1 (K), U2.6 (RA4)
/MCU/MISO: TP5.1, U2.15 (RC4); also elsewhere on the board
/MCU/MOSI: TP6.1, U2.16 (RC5); also elsewhere on the board
/MCU/OSC1: C3.1, U2.9 (RA7/OSC1), Y1.1
/MCU/OSC2: C4.1, U2.10 (RA6/OSC2), Y1.2
/MCU/RESET: U2.18 (RC7); also elsewhere on the board
/MCU/SCLK: TP4.1, U2.14 (RC3); also elsewhere on the board
/MCU/~MCLR: J1.5, R1.2, U2.1 (~MCLR)
CANH: U1.7 (CANH); also elsewhere on the board
CANL: U1.6 (CANL); also elsewhere on the board
GND: C1.2, C2.1, C3.2, C4.2, J1.3, U1.2 (VSS), U1.8 (STBY), U2.8 (VSS), U2.19 (VSS); also elsewhere on the board
unnamed: D1.2 (A), R2.1
unnamed: D2.2 (A), R3.1
unnamed: D3.2 (A), R4.1
unnamed: R16.2, U2.25 (RB4)
unnamed: R11.1, U2.26 (RB5)

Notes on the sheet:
CAN
Crystal
Programming Header
Standard Waterloo Rocketry PIC18 Setup
Programmable Test LED's



Board: 4 copper layers, 63.4 x 66.3 mm, 106 parts (31 on the bottom side), 69 nets.

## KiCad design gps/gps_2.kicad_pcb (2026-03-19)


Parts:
C1, C7, C9, C10, C13: 22pF; C_0603_1608Metric_Pad1.08x0.95mm_HandSolder
C2, C6, C14: 0.1uF; C_0603_1608Metric_Pad1.08x0.95mm_HandSolder
C3: 10uF; C_0603_1608Metric_Pad1.08x0.95mm_HandSolder
C4, C5: 1uF; C_0603_1608Metric_Pad1.08x0.95mm_HandSolder
C8: 2.2uF; C_0603_1608Metric_Pad1.08x0.95mm_HandSolder
C11, C12: 26pF; C_0805_2012Metric_Pad1.18x1.45mm_HandSolder
D1: WHITE; LED_1206_3216Metric_Pad1.42x1.75mm_HandSolder
D2: RED; LED_1206_3216Metric_Pad1.42x1.75mm_HandSolder
D3: BLUE; LED_1206_3216Metric_Pad1.42x1.75mm_HandSolder
D4: KDZVTR3.6B; D_SOD-123F
F1: 0ZCM0008FF2G; Fuse_0603_1608Metric_Pad1.05x0.95mm_HandSolder
H1, H2, H3, H4: MountingHole; MountingHole_3.2mm_M3_Pad
J1: Programming Header; PinSocket_5x2.54_SMD_90deg_952-3198-1-ND
J2: G125-MH104M4-04AD000P; connector_Harwin_G125-MH104M4-04AD000P
J3: EMPCB.SMAFSTJ.B.HT; TAOGLAS_EMPCB.SMAFSTJ.B.HT
L1, L2: 47nH; L_0603_1608Metric_Pad1.05x0.95mm_HandSolder
R1: 100R; R_0603_1608Metric_Pad0.98x0.95mm_HandSolder
R2, R3: 10k; R_0603_1608Metric_Pad0.98x0.95mm_HandSolder; not fitted
R4: 10K; R_0603_1608Metric_Pad0.98x0.95mm_HandSolder
R7, R8: 160; R_0603_1608Metric_Pad0.98x0.95mm_HandSolder
R9: 200mR; R_0603_1608Metric_Pad0.98x0.95mm_HandSolder
TP1: RX; TestPoint_THTPad_1.0x1.0mm_Drill0.5mm
TP2: TX; TestPoint_THTPad_1.0x1.0mm_Drill0.5mm
TP3, TP4: 36-5001-ND; TestPoint_Keystone_5000-5004_Miniature
U1: M10578-A2; QFN16_M10578_ANT
U2: PIC18F26K83; SOIC-28W_7.5x18.7mm_P1.27mm
U3: MCP2562; SOIC-8_3.9x4.9mm_P1.27mm
U4: SPX3819M5-L-3-3; SOT-23-5_HandSoldering
U5: INA180; SOT-23-5_HandSoldering
Y1: ABM8G-12.000MHZ-18-D2Y-T; Crystal_SMD_Abracon_ABM8G-4Pin_3.2x2.5mm

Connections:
+3V3: C1.1, C2.2, C5.1, C7.1, C8.1, C14.1, D4.1 (K), J1.4, R4.1, U1.14 (BV), U1.15 (VCC), U2.20 (VDD), U3.5 (VIO), U4.5 (OUT)
+5V: C3.1, C4.1, C6.1, R9.1, U3.3 (VDD), U4.1 (IN), U4.3 (EN), U5.4 (IN-), U5.5 (VS)
/BLUE_LED: D3.2 (A), U2.11 (RC0)
/CANH: J2.1 (CANH), U3.7 (CANH)
/CANL: J2.2 (CANL), U3.6 (CANL)
/CAN_RX: TP4.1, U2.25 (RB4), U3.4 (RXD)
/CAN_TX: TP3.1, U2.26 (RB5), U3.1 (TXD)
/CURR_SENSE: U2.22 (RB1), U5.1 (VO)
/FIX: R1.1, U1.13 (FIX), U2.7 (RA5)
/ICSPCLK: J1.1, U2.27 (RB6/ICSPCLK)
/ICSPDAT: J1.2, U2.28 (RB7/ICSPDAT)
/OSC1: C11.1, U2.9 (RA7/OSC1), Y1.3 (OSC2)
/OSC2: C12.1, U2.10 (RA6/OSC2), Y1.1 (OSC1)
/PIC_RX_GPS_TX: C9.2, L1.2, TP2.1, U2.14 (RC3)
/PIC_TX_GPS_RX: C10.2, L2.2, TP1.1, U2.13 (RC2)
/PPS: U1.6 (PPS), U2.15 (RC4)
/RED_LED: D2.2 (A), U2.12 (RC1)
/RF_IN: J3.1, U1.3 (RFIN)
/~HWR: C13.2, U1.7 (HWR), U2.16 (RC5)
/~MCLR: J1.5, R4.2, U2.1 (~MCLR)
GND: C1.2, C2.1, C3.2, C4.2, C5.2, C6.2, C7.2, C8.2, C9.1, C10.1, C11.2, C12.2, C13.1, C14.2, D1.1 (K), D4.2 (A), H1.1, H2.1, H3.1, H4.1, J1.3, J2.D (GND), J3.SH1, J3.SH2, J3.SH3, J3.SH4, R2.2, R3.2, R7.2, R8.2, U1.1 (GND), U1.2 (GND), U1.4 (GND), U1.5 (GND), U1.16 (GND), U2.8 (VSS), U2.19 (VSS), U3.2 (VSS), U3.8 (STBY), U4.2 (GND), U5.2 (GND), Y1.2 (GND), Y1.4 (GND)
unnamed: D1.2 (A), R1.2
unnamed: D2.1 (K), R7.1
unnamed: D3.1 (K), R8.1
unnamed: F1.1, J2.C (+5V)
unnamed: R2.1, U1.11 (E2)
unnamed: R3.1, U1.12 (E3)
unnamed: L2.1, U1.9 (RX)
unnamed: L1.1, U1.10 (TX)
unnamed: F1.2, R9.2, U5.3 (IN+)

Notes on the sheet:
Pull Down Resistors Added to E2/E3 Provide Baud Rate Control
GAIN: 100 V/V
Changed Oscillator
Diode Eliminated
Rough Documentation on Decisions
Fuse Changed To 0603 Footprint
All Component Footprints Changed to 0603
Protection in case someone uses the Pickit to supply 5V power 3.8V zener 1W
Footprint Changed to Reflow One
C12=C11=2*(CL-Cstray) CL=18pF, Cstray=5pF C12=C11=26pF https://microchip.my.site.com/s/article/Calculating-crystal-load-capacitor
max Id = 200 mA
Pins Rearranged
GRM033R61 E224ME01D



Board: 2 copper layers, 54.3 x 28.9 mm, 45 parts (18 on the bottom side), 30 nets.

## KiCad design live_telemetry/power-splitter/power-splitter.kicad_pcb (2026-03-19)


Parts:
H1, H2: MountingHole_Pad; MountingHole_3.2mm_M3_Pad_Via
J1, J2, J3: Conn_Coaxial_Small; TAOGLAS_EMPCB.SMAFSTJ.B.HT
R1: 100R; R_0603_1608Metric_Pad0.98x0.95mm_HandSolder
U1: PD0810J5050S2HF; DigiKey_Part_Number 1173-1093-1-ND

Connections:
GND: H1.1, H2.1, J1.2 (Ext), J2.2 (Ext), J3.2 (Ext), U1.1, U1.3, U1.5
unnamed: J1.1 (In), U1.2 (IN)
unnamed: J2.1 (In), R1.1, U1.4 (OUT1)
unnamed: J3.1 (In), R1.2, U1.6 (OUT2)


Board: 2 copper layers, 29.0 x 16.6 mm, 7 parts (0 on the bottom side), 4 nets.

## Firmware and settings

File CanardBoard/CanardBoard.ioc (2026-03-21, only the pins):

Mcu.UserName=STM32H733VGTx
PA0.GPIO_Label=SD_CMD
PA0.Signal=SDMMC2_CMD
PA1.GPIO_Label=VSENS_RKT
PA1.Signal=ADC1_INP17
PA10.GPIO_Label=SERVO2_RX
PA10.Signal=USART1_RX
PA11.GPIO_Label=USB_D-
PA11.Signal=USB_OTG_HS_DM
PA12.GPIO_Label=USB_D+
PA12.Signal=USB_OTG_HS_DP
PA13(JTMS/SWDIO).GPIO_Label=DEBUG_SWDIO
PA13(JTMS/SWDIO).Signal=DEBUG_JTMS-SWDIO
PA14(JTCK/SWCLK).GPIO_Label=DEBUG_SWCLK
PA14(JTCK/SWCLK).Signal=DEBUG_JTCK-SWCLK
PA15(JTDI).GPIO_Label=S_CAN_STB
PA15(JTDI).Signal=GPIO_Output
PA2.GPIO_Label=VSENS_CHG
PA2.Signal=ADCx_INP14
PA3.GPIO_Label=VSENS_USB
PA3.Signal=ADCx_INP15
PA4.GPIO_Label=ISENS_BAT2
PA4.Signal=ADCx_INP18
PA5.GPIO_Label=ISENS_BAT1
PA5.Signal=ADCx_INP19
PA6.GPIO_Label=FLASH_IO3
PA6.Signal=OCTOSPIM_P1_IO3
PA7.GPIO_Label=FLASH_IO2
PA7.Signal=OCTOSPIM_P1_IO2
PA8.GPIO_Label=BAR_SCL
PA8.Signal=I2C5_SCL
PA9.GPIO_Label=SERVO2_TX
PA9.Signal=USART1_TX
PB0.GPIO_Label=FLASH_IO1
PB0.Signal=OCTOSPIM_P1_IO1
PB1.GPIO_Label=FLASH_IO0
PB1.Signal=OCTOSPIM_P1_IO0
PB10.GPIO_Label=ADI_SCL
PB10.Signal=I2C2_SCL
PB11.GPIO_Label=ADI_SDA
PB11.Signal=I2C2_SDA
PB12.GPIO_Label=M_CAN_RX
PB12.Signal=FDCAN2_RX
PB13.GPIO_Label=M_CAN_TX
PB13.Signal=FDCAN2_TX
PB14.GPIO_Label=SD_D0
PB14.Signal=SDMMC2_D0
PB15.GPIO_Label=SD_D1
PB15.Signal=SDMMC2_D1
PB2.GPIO_Label=FLASH_CLK
PB2.Signal=OCTOSPIM_P1_CLK
PB3(JTDO/TRACESWO).GPIO_Label=SD_D2
PB3(JTDO/TRACESWO).Signal=SDMMC2_D2
PB4(NJTRST).GPIO_Label=SD_D3
PB4(NJTRST).Signal=SDMMC2_D3
PB5.GPIO_Label=IMU_INT2
PB5.Signal=GPXTI5
PB6.GPIO_Label=IMU_SCL
PB6.Signal=I2C1_SCL
PB7.GPIO_Label=IMU_SDA
PB7.Signal=I2C1_SDA
PB8.GPIO_Label=MAG_SCL
PB8.Signal=I2C4_SCL
PB9.GPIO_Label=MAG_SDA
PB9.Signal=I2C4_SDA
PC0.GPIO_Label=M_SYNC_OUT
PC0.Signal=GPIO_Input
PC1.GPIO_Label=SD_CLK
PC1.Signal=SDMMC2_CK
PC10.GPIO_Label=SERVO1_TX
PC10.Signal=UART4_TX
PC11.GPIO_Label=SERVO1_RX
PC11.Signal=UART4_RX
PC13.GPIO_Label=LED_R
PC13.Signal=GPIO_Output
PC14-OSC32_IN.GPIO_Label=LED_G
PC14-OSC32_IN.Signal=GPIO_Output
PC15-OSC32_OUT.GPIO_Label=LED_B
PC15-OSC32_OUT.Signal=GPIO_Output
PC2_C.GPIO_Label=ISENS_3V3
PC2_C.Signal=ADC3_INP0
PC3_C.GPIO_Label=ISENS_5V
PC3_C.Signal=ADC3_INP1
PC4.GPIO_Label=VSENS_BAT1
PC4.Signal=ADCx_INP4
PC5.GPIO_Label=VSENS_BAT2
PC5.Signal=ADCx_INP8
PC6.GPIO_Label=PWR_EN
PC6.Signal=GPIO_Output
PC7.GPIO_Label=BAT_FLT1
PC7.Signal=GPIO_Input
PC8.GPIO_Label=BAT_FLT2
PC8.Signal=GPIO_Input
PC9.GPIO_Label=BAR_SDA
PC9.Signal=I2C5_SDA
PD0.GPIO_Label=S_CAN_RX
PD0.Signal=FDCAN1_RX
PD1.GPIO_Label=S_CAN_TX
PD1.Signal=FDCAN1_TX
PD10.GPIO_Label=M_CAN_STB
PD10.Signal=GPIO_Output
PD11.GPIO_Label=R_CAN_STB
PD11.Signal=GPIO_Output
PD12.GPIO_Label=R_CAN_RX
PD12.Signal=FDCAN3_RX
PD13.GPIO_Label=R_CAN_TX
PD13.Signal=FDCAN3_TX
PD5.GPIO_Label=SERVO4_TX
PD5.Signal=USART2_TX
PD6.GPIO_Label=SERVO4_RX
PD6.Signal=USART2_RX
PD7.GPIO_Label=IMU_INT1
PD7.Signal=GPXTI7
PD8.GPIO_Label=MOVELLA_TX
PD8.Signal=USART3_TX
PD9.GPIO_Label=MOVELLA_RX
PD9.Signal=USART3_RX
PE0.GPIO_Label=INT_MAG
PE0.Signal=GPXTI0
PE1.GPIO_Label=INT1_MAG_ACCEL
PE1.Signal=GPXTI1
PE10.GPIO_Label=FLASH_CS
PE10.Signal=GPIO_Output
PE11.GPIO_Label=PWM2
PE11.Signal=S_TIM1_CH2
PE12.GPIO_Label=ADC_INT
PE12.Signal=GPXTI12
PE13.GPIO_Label=PWM3
PE13.Signal=S_TIM1_CH3
PE14.GPIO_Label=PWM4
PE14.Signal=S_TIM1_CH4
PE15.GPIO_Label=ADXL_INT
PE15.Signal=GPXTI15
PE2.GPIO_Label=ADXRS_ST1
PE2.Signal=GPIO_Output
PE3.GPIO_Label=ADXRS_ST2
PE3.Signal=GPIO_Output
PE4.GPIO_Label=CHG_MUX_EN
PE4.Signal=GPIO_Output
PE5.GPIO_Label=EN_EXT_5V
PE5.Signal=GPIO_Output
PE6.GPIO_Label=PG_EXT_5V
PE6.Signal=GPIO_Input
PE7.GPIO_Label=SERVO3_RX
PE7.Signal=UART7_RX
PE8.GPIO_Label=SERVO3_TX
PE8.Signal=UART7_TX
PE9.GPIO_Label=PWM1
PE9.Signal=S_TIM1_CH1
PH0-OSC_IN.GPIO_Label=OSC_IN
PH0-OSC_IN.Signal=RCC_OSC_IN
PH1-OSC_OUT.GPIO_Label=M_SYNC_IN1
PH1-OSC_OUT.Signal=GPIO_Output

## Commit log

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2018-09-11 Schematic review changes
    - swap signals on RC4, RA5 (pic16f)
    - add oscillator to 26k83
    - break out usb connector
    - break out some unused 26k83 pins
    Also:
    - break out can bus
    - add missing decoupling caps
    [PIC16F1455.sch, PIC18F26K83.sch, picdev.sch]
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2018-09-15 First stab at schematic for rocket logger board
    Schematic isn't very pretty, and is missing some component values, but
    should mostly be done. Board features:
    - 2 SD cards driven by separate SPI modules
    - A dsPIC33EP512GP502 micro (super overkill)
    - CAN interfacing
    - Buck converter from bus to 5v, LDO from 5v to 3v3
    - Current Sense amp for total current draw from bus power
    - Programming header
    - External oscillator
    - 2 Debug LEDs
    [SDcard.sch, logger_can.sch, logger_power.sch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]
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2018-09-16 First stab at schematic for radio/power control board
    Schematic is missing some component values, mostly for the SMPS. Board
    features:
    - An Xbee (surface mount), with logic level shifting
    - A PIC18F26K83 (with programming header)
    - Two MOSFETs to cut power from the bus lines (needs to be breadboarded)
    - 3 Debug LEDs
    - Current sense amplifiers on current from battery and current to bus
    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
    [power.sch, radio.kicad_pcb, radio.sch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]
2018-09-17 Fixes from Alex's review
    - Current sense amps powered from 5v rail, not 3v3
    - reorder bus connector to power, ground, canh, canl
    - Switch debug LEDs from sourcing current to sinking current
    - Change MCLR to ~MCLR
    [power.sch, radio.sch, xbee_module.sch]
2018-09-18 Minor review fix on USB dog
    Remove the bus power connector on the CAN header, it now only contains
    ground, CANH and CANL. Also minor silkscreen edits to show which pins
    are CANH, CANL, GND, and ~MCLR.
    [usbdbg-B.Cu.gbl, usbdbg-B.Mask.gbs, usbdbg-Edge.Cuts.gm1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]
2018-09-21 Increase Font size on USB Dog's silkscreen layer
    E5 SDC PCB centre can't print text on silkscreen narrower than .35mm
    and shorter (height) than 2mm, ie really big text. This commit
    increases the font size of all text, including part numbers (R4, U2,
    whatever). The test point part numbers had to be removed from
    silkscreen because there was no room for them, but all other parts are
    still labelled.
    No copper, solder mask, or mechanical layers were changed in this
    commit.
    [usbdbg.kicad_pcb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]
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2018-09-23 Injector schematic review changes
    - fix resistor value for current amp
    - remove test points
    - add 12V rail to CAN connector
    [mcu.sch, power.sch]
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2018-09-25 Review Fixes
    Changes in this commit:
    1. Change power symbol +VBATT to +12V for consistency
    2. Replace 4 pin bus connector with 5 pin (pinout 1-5 = 12v, 5v, gnd, canh,
    canl)
    3. Move current limiting resistor on bus enable line so it's in series with
    three nmos's
    4. Replace Q2 (transistor that pulls down the gate of the p-channel mosfets)
    with a mosfet instead of a bjt
    5. pull down bus enable line, so the gates don't explode
    [power.sch, radio.sch, xbee_module.sch]
2018-09-25 Review Tweaks
    Move explanation text that was in a terrible spot, replace a DNP
    resistor with a 10K resistor because it turns out the resistor
    shouldn't have been DNP.
    [power.sch, xbee_module.sch]
2018-09-26 USB Debug update - ready for review for production version (not usbdog)
    Remove the 0ohm resistors from USB power to 5V rail and from CAN
    ground to ground plane. These were unneccessary, a wire does just
    fine.
    Replace the CAN bus connector with a more standard 5 pin one. The usb
    board should use the same connector as every other board, now it
    can. There's a new jumper that allows you to power the CAN bus from
    the USB board's 5V rail, in case you're doing an integration test or
    something and you want to do that.
    [usbdbg.sch]
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2018-09-26 Rocketlog - Review Changes
    - change capacitor on SD card power rail to 4.7uF. Not sure of proper value,
    but decoupling definitely is necessary (SD cards draw a lot of current).
    - Remove the SMPS, run the board off 5V CAN rail (3v3 LDO is still there)
    - Replace 4pin CAN connector with standard pinout 5pin connector
    - Put current sense amplifier on 5V rail instead of VBATT rail
    - Annotate the schematic (sorry)
    - change MCLR to ~MCLR
    - add polyfuse on 5V CAN bus rail
    - remove US style resistors, all resistors now EU metric apologist style
    - Set R_Sense and current gain values, full scale at 266mA (is this good?)
    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
    [SDcard.sch, logger_power.sch, rocketlog.sch]
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2018-09-29 Vent board review changes
    - fix PMOS symbol
    - make voltage divider less fat
    - NC unused 12V rail
    TODO: failsafe for the DACs
    [la_driver.sch, power.sch]
2018-09-29 Radio board Review fix - Add new SMPS
    Running the Diodes incorporated AN1509 SMPS now, using component
    values sourced from their datasheet and application note.
    [power.sch]
2018-09-30 Fix fail-safe control on vent
    Add a linear regulator to power the comparators and DACs off the same
    battery as the linear actuator.
    [la_driver.sch, power.sch]
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2018-10-03 Radio board: Fix SMPS, it was reverted to an older version in recent merge commit
    [power.sch]
2018-10-03 Radio board: Create BOM, assign footprints
    It is not guaranteed that all footprints are correct, I still need to
    check that. BOM does not contain resistors or caps, but it does
    contain connectors and the inductor. All parts are from digikey.
    [power.sch, radio.sch, radio_bom.csv]
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2018-10-04 Radio board: Generate netlist and do preliminary layout.
    Noticed that one footprint was misassigned - the MCP2562 was listed as
    a 14 pin package when it should have been 8 pins
    Done preliminary sizing. I believe that if the board is packed very
    tightly, it can be made as a 6x7cm 6/6 2-layer board. Might be that
    I'm overoptimistic, the preliminary layout doesn't even fit in that
    space, but heck, I'm hopeful.
    [radio.kicad_pcb, radio.sch]
2018-10-04 Logger: Initial ballpark layout for logger, to see how big it should be
    Some footprints are not final ones - CAN connector is wrong, crystal
    is wrong, current sense resistor is probably wrong, SD card holder is
    wrong. These are just ballpark estimates so that we can get an idea of
    the order of magnitude of the size of the final board.
    [SDcard.sch, logger_power.sch, rocketlog.kicad_pcb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]
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2018-10-09 Logger Board PCB Review 1 changes
    - Move C2 further from U1
    - Space out F1, R5, U4 and C8
    - Silkscreen rearrangements to make it pretty
    - Replace J1 (SMT programming header) with a 90 degree connector
    - Replace U3 with hand soldering footprints
    - Turn mounting holes into plated holes
    - Remove daisy chaining through pads. I hope I got all of them, please check
    - Get rid of the power trace running through the SD card housing....
    - Move SD card holders down, so the SD cards don't overhand the board
    - Add rocketry logo to front silkscreen for that sweet sweet brand value
    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
    [logger_power.sch, rocketlog.kicad_pcb, rocketlog.sch]
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2018-11-03 Injector fab review changes
    - delete paste files
    - make mounting hole spacing nicer
    - name it
    - move the connectors closer to the edge of the board
    - move trace away from R15, R17
    - move trace into center of R13 (:|)
    - reduce soldermask clearance
    - regenerate gerbers
    [vent-B.Cu.gbl, vent-B.Mask.gbs, vent-B.Paste.gbp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]
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2018-11-04 Last minute review fixes
    - change routing around U1
    - update zone clearance
    - updated soldermask clearance
    [injector.kicad_pcb]
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2018-11-04 Injector fab review changes:
    - rotate R1 silkscreen
    - move the power transistors up
    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
    [injector-B.Cu.gbl, injector-B.Mask.gbs, injector-B.Paste.gbp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]
2018-11-04 Logger Board: Fab review 1 fixes
    Changes fixed in this commit:
    - Make mounting holes 1.5in square because I ain't no metric apologist
    - Make programming header not overhang bottom right mounting hole
    - Change MCLR to ~MCLR on silkscreen
    - Move C1 closer to MCU
    - Move C3 further from MCU
    - Add 10uF capacitor on CAN transceiver (C11)
    Generate gerbers to reflect these changes
    [SDcard.sch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]
2018-11-04 Radio Board: Fab review 1 fixes
    - Reduce min soldermask width (6mil) so there isn't weird briding
    - Make mounting hole layout imperial (1.75"x1.875")
    - Name it. It now has a terrible name that I didn't get to pick. Harrumph.
    - Change soldermask clearance down to 2mil
    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
    [radio-B.Cu.gbl, radio-B.Mask.gbs, radio-B.SilkS.gbo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]
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2018-11-11 Fix gps lib issues
    - set canhw as a project specific library
    - update library for gps component
    [gps.sch]
2018-11-22 WIP sensor board
    TODO:
    - check common mode on rtd amp. Might need to swap that out.
    - put in a 15V regulator.
    [analog_sense.sch, digital_sense.sch, mcu.sch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]
2018-11-22 Sensor board review changes
    - annotate everything
    - fix symbol library mapping
    - fix debug header orientation
    - add extra decoupling cap to mcu
    - add a couple debug leds
    - add 15V regulator (tht)
    - add sensor comments
    [analog_sense.sch, digital_sense.sch, mcu.sch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]
2018-11-22 Update digital sensor suite
    Swap out our old IMUs with a pair of BMX055s. Add all the interfacing
    required for that.
    [analog_sense.sch, digital_sense.sch, mcu.sch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]
2018-11-22 Replace IMU cause Jacob wanted to
    New IMU has better magnetometer sensitivity
    [digital_sense.sch, mcu.sch, power.sch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]
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2018-11-22 Sensor board review changes
    - reroute some traces to make pours cleaner
    - fix soldermask clearance
    [sensors.kicad_pcb]
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2018-11-22 Sensor fab review 2 fixes
    - move some traces and vias around
    - remove some daisy chaining
    - add silkscreen to connectors
    - add an actual edges layer
    [sensors-B.Cu.gbl, sensors-B.Mask.gbs, sensors-B.SilkS.gbo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]
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2018-12-05 Addressed Alex's comments: Fixed Level shifters, specified directions of the signals correctly. Added Pull-up resistors for the level shifters Switched from SPI to UART, fixed nessesary connections G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
    [mcu.sch, module.sch, power.sch]
2018-12-08 Addressed Alex's issues: Replaced 5V to 3v3 level shifter with 2 voltage dividers Fixed Hierarchical labels for the gps Renamed and clarified some connections
    [gps.sch, mcu.sch, module.sch]
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2018-12-21 Addressed changes: Re-added the 2.2 resistors in series with the 0ohm resistor Accidentally wired the gps-board into self start mode when changing from SPI to UART. Reverted this change. Connected PI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
    [gps.sch, mcu.sch, module.sch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]
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2019-01-21 Vent: fix schematic libraries, minor pcb tweaks
    - Change all components supposedly in vent-rescue.lib back to canhw.lib
    where they should be.
    - Rotate Q3 and Q4 so they match Q5 and Q6
    - Clean up traces
    [la_driver.sch, mcu.sch, power.sch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]
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2019-01-23 Address final changes: Add 0 ohm resistor in the Enable pin of U4 (the new level shifter) Replace the old voltage divider with a bidirection level shifter Modify library as necessary
    [mcu.sch, module.sch]
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2019-03-17 Addressed Adam's comments. Disregarded comments that were related to Traces since I wanted to confirm the layout.
    Comments Addressed:
    Denoted all capacitance with capital 'F'
    Removed net label on pin 5 of U3
    Defined Edge cuts
    Changed layout such that the silkscreens doint end up under pads
    Changed mounting holes to be plated
    Trace-related comments ignored (until layout is confirmed:
    All the DRC errors
    Power Plane definition
    Other ignored comments:
    Hierachal sheets (too lazy to change it at this point. I also personally think it's easier to look at
    Use of TVS diodes (No other board in CANBus has it)
    different PIC ( I believe were using this pic bc we already have programmed drivers for it)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
    [_saved_gps.sch, _saved_mcu.sch, module.sch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]
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2019-03-23 Sensor mini: Add analog stuff
    Adds one thermistor and the tank pressure sensor to sensor_mini.
    Required making the board a quarter inch wider. This commit updates the
    PCB and the schematic.
    Note that while all the traces are there (DRC mostly passes (IMU is too
    small for 6mil DRC), and everything is connected), it isn't done. The
    traces are not great, much improvement possible. Also, it's likely that
    we'll be swapping the integrated IMU and gyro for just a discrete gyro,
    since it was a bitch to work with on the big sensor board.
    [analog.sch, digital_sense.sch, mcu.sch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]
2019-03-26 Addressed Adam and Alex's comments. General fixes:
    Switched to a PIC that supports 3V3 and removed all level shifting
    Fixed any traces >= 90 degrees
    Added silkscreen for Team logo and LED
    Add more space between components and reduced the board's size
    [_saved_mcu.sch, gps.kicad_pcb, gps.sch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]
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2019-04-07 Addressed Alex comments Fixed all DRC errors where a ground fill wasn't connected Alligned a bunch of IC to make thge board look prettier Fix silkscreens
    [gps.kicad_pcb]
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2019-04-09 Review changes: Aaron & Julie
    - Fatten up some traces
    - Connect CSB pin on U10 to VDD
    - Remove some wonky traces
    - Change clearance to 5 mil
    - Rotate some caps to be cuter
    [digital_sense.sch, sensors.kicad_pcb]
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2019-04-14 Address Alex's comments
    Fixed weird traces.
    Did not fix the unecessary ground via. Awaiting comment
    [gps.kicad_pcb]
2019-04-18 Review changes (Aidan, Aaron)
    - fix some daisy chaining
    - if you liked it then you shoulda put a logo on it
    [sensors.kicad_pcb]
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2019-04-18 DFM changes
    - Increase zone to copper clearance to 8 mil
    - Add 2 mm fillet to zones
    - Fix some wonky traces
    [sensors-B.Cu.gbl, sensors-B.Mask.gbs, sensors-B.SilkS.gbo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]
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2019-04-19 Switch microcontroller to run off of 3V3
    This needs very serious review. I made these changes quickly, while
    tired, and while currently eating dinner. Please look very closely at
    everything, whoever winds up reviewing this.
    The reason the PIC needs to run off of 3v3 is so that it can interface
    with the GPS chip over UART without level shifting (GPS runs off of
    3v3). Not sure if I'm just missing something or how this got this far
    into reviews without someone noticing. If I'm just off base in thinking
    this change needs to be made, please revert the commit.
    Itemized list of changes:
    schematic:
    - Replace 5v with 3v3 on:
    - MCLR pullup
    - Microcontroller VDD
    - programming header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
    [gps-B.Cu.gbr, gps-B.Mask.gbr, gps-B.SilkS.gbr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]
2019-04-19 Made further changes to the recent reivew (that fixed a major issue with the PIC
    Redrew serveral traces.
    Removed unessesary vias
    Checked over all data sheets one last time to ensure I didn't make another mistake.
    [gps-B.Cu.gbr, gps-B.Mask.gbr, gps-B.SilkS.gbr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]
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2020-03-03 Fix level shifting circuit, improve layout of altimiters for better readability, and other small fixes
    [altimeters.sch, power.sch, recovery_CAN.sch]
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2020-03-03 Fix board size to be 2.8 inch square, generate final gerber files for fab.
    [recovery_CAN-B.Cu.gbl, recovery_CAN-B.Mask.gbs, recovery_CAN-B.SilkS.gbo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]
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2020-03-03 Fix voltage mismatches, LED voltages, and add relative file path for canlib
    -Programming header switched from 5V to 3V3
    -LEDs switched from 5V to 3V3
    -Relative file path added for transmitter and receiver for canlib
    [power.sch, radio.sch, telemetry_receiver.sch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]
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2020-03-03 Add copper pours and address Jared's comments
    -Still haven't fixed CAN TX/RX lines running through OSC1&2
    -Still need to add team logo
    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
    [telemetry_receiver.kicad_pcb, telemetry_transmitter.kicad_pcb]
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2020-03-03 Add initial tracing
    Definitely not super happy with the first round but I wanted something
    to get out for review so we can get this started. I mentioned in slack
    we needed an actual part number but it won't affect the number of pads
    on Q1 so it should be easy to replace even if the footprint changes.
    [vent.kicad_pcb]
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2020-03-03 Fix symbol library mapping for vent
    Make symbols use canhw.lib instead of rescue library.
    [mcu.sch, power.sch, valvectrl.sch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]
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2020-03-03 Fix daisy-chained trace on current amp and gennerate zip file for gerbers.
    [fill_sensing-B.Cu.gbr, fill_sensing-B.Mask.gbr, fill_sensing-B.SilkS.gbr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]
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2020-03-03 Fix symbol mapping in fill sensing
    Use symbols from canhw instead of rescue libraries.
    [fill_sensing.sch]
2020-03-03 Add base schematic for GPS V2 Remove all 0 ohm resistors Remove GPS Module LED and one of the PIC debug LED Remove external Oscillator Remove GPS_RX_PIC_TX line
    To be added:
    External Antenna for Module
    External connector for the board
    More stuff. Schematic is incomplete
    [gps_2.kicad_pcb, gps_2.sch]
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2020-03-03 Address Aaron's comments: - Fix inductor values to align with datasheet recomendations - Change C1 to 2.2uF to fix off by 10 - Change R7, R8 to 160 to fix current flow on D2, D3 - Change labels on D2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
    [gps_2.sch]
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2020-03-03 Add third round of layout: - Replace SMA connector for horizontal connection and clearance - Move GPS away from Y1 to reduce interferance - Increase component spacing to ease soldering
    [gps_2.kicad_pcb, gps_2.sch]
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2020-03-03 Increase assembly and fabrication ease: - Move C2, R7, R8 to allow solderability - Move 5V trace and R9-U5 trace to add >6 mils clearance
    [gps_2.kicad_pcb]
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2020-03-03 Partial review fixes
    - Move C9, C10 to be inline
    - Move LEDs down to leave more room for soldering
    [rocketlog.kicad_pcb]
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2020-03-03 Change oscillator caps to 27pF
    There aren't actually any 26pF caps on Digikey and we've been using 25
    and 27pF instead. Changed in all schematics.
    [fill_sensing.sch, gps_2.sch, mcu.sch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]
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2020-05-21 Switch minisensor to run off 3v3, not 1v8
    We weren't able to program the microcontroller on minisensor when it was
    running on 1v8 VDD, so we swapped the voltage regulator for a 3v3
    regulator and it all worked fine. The original reason for 1v8 was that
    there was a digital sensor we wanted to use that couldn't run on 3 volts
    (the ICM-20948). This sensor got removed in the move from macrosensor to
    minisensor, so there's no reason not to use 3v3 on minisensor. The three
    digital sensors on the latter all work at 3v3, datasheets below:
    - https://www.te.com/commerce/DocumentDelivery/DDEController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
    - https://www.st.com/content/cc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
    [analog.sch, digital_sense.sch, mcu.sch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]
2020-05-21 Update minisensor PCB from netlist file
    I had previously updated the minisensor schematic to run off of 3v3
    instead of 1v8, but hadn't updated the PCB. So this fixes that.
    [sensors.kicad_pcb]
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2020-10-16 Finish initial routing of arming V2 including switching to 4 laer board and improving clearance on harwin connectors.
    [power.sch, recovery_CAN.kicad_pcb]
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2021-03-06 Add Jumper Lables and fix 5V supply to draw strait from bus.
    [power.sch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]
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2022-02-07 Changed IMU to MPU-6050
    Removed ICM-20789 from schematic / symbol library, replaced it with MPU-6050
    [digital_sense.sch]
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2023-01-30 Begin addressing PR comments
    Added values, replaced 5->3.3regulator, added decoupling caps, fixed barometer address, accommodated 3-pin connectors, added LEDs, addedd interrupt pin, changed inductor formatting
    [analog.kicad_sch, digital_sense.kicad_sch, mcu.kicad_sch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]
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2023-01-30 Annotated schematic, added part numbers for diodes and fets, removed the LTC4414 ideal diode source selector and replaced it with a diode OR circuit.
    [Battery_charger.kicad_sch, Power.kicad_sch, charging_on_the_pad.kicad_sch]
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2023-01-30 Swapped the battery charger and mosfets for ones that are more easily soldered
    [B1047AS-2R2N=P3.STEP, Battery_charger.kicad_sch, charging_on_the_pad.kicad_pcb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]
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2023-01-30 board is 95% finished, need to make a few small changes and do via stitching, and then fix the silkscreen.
    [charging_on_the_pad.kicad_pcb]
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2023-01-30 implemented jack's and randy's feedback. currently, the only thing left to do is decide what I will do with an issue regarding the ICH/EN pin.
    [Battery_charger.kicad_sch, Power.kicad_sch, charging_on_the_pad.kicad_pcb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]
2023-01-30 all fixes have been made. Issue with the ICH/EN pin has also been fixed (changed the battery charger's CSR and increased charging current to 300mA. Also changed R24 to 220R for BOM count. Ready for l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
    [Battery_charger.kicad_sch, Power.kicad_sch, charging_on_the_pad.kicad_pcb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]
2023-01-30 fixed jack's point #5, connecting VCC (always ON) to the connector and not 13V (only ON when 24V is connected)
    [charging_on_the_pad.kicad_pcb, charging_on_the_pad.kicad_sch, charging_on_the_pad.step]
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2023-01-30 swapped a 1206 cap on 0805 cap. generated gerbers. changed PN for 5A fuse on schematic. PCB looks good, only change was the footprint swap.
    [Power.kicad_sch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]
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2023-12-16 fuse to smd for real this time, netlabel connection points fixed, motor now connected to +BATT rather than +13V
    [Power.kicad_sch, charging_on_the_pad.kicad_sch]
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2023-12-18 fixed ICHG_EN, FET between +BATT and MOTOR_V, Resistor Divider on 13V buck
    [Battery_charger.kicad_sch, Power.kicad_sch, charging_on_the_pad.kicad_sch]
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2023-12-29 actually fixed 9 this time, also fixed the rest of 11 by changing the fuse (no new footprint needed now)
    [Power.kicad_sch]
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2024-03-11 fixed most errors, only remaining errors are unfixable (two pads on a chip too close together)
    [charging_on_the_pad.kicad_pcb]
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2024-03-19 USB Debug Respin (#71)
    * Updated usb debug schematic for review
    * - Added data sheet for fuse
    - Changed symbols for USB-B and fuse/fuse holder
    - Deleted duplicate files
    * - Added symbol libraries for real this time
    * Added name to schematic
    Deleted unnecesary files
    Updated .gitignore
    * Added kikad symbol
    * Made small fix with symbol library file path
    * - updated symbols
    - CAN connector now uses 4 pin smd
    - made several minor changes to presentation. Would make for a nice game of spot the differences.
    * - Updated footprints
    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
    [usbdbg-B_Cu.gbl, usbdbg-B_Mask.gbs, usbdbg-B_Paste.gbp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]
2024-03-19 Propulsion board (#72)
    * Add PropulsionBoard
    * Add propulsion board
    * Address Jack's comment on the propulsion board
    * Propulsion Board Address Comments Final Revision
    * Propulsion Board Address Jack's Comments Final Revision
    * Revert "Add propulsion board"
    This reverts commit 4b1eeec09cc4060f319076640d95fd3068bfa2a7.
    * propulsion board address second review changes
    * addressing latest comments
    * propulsion board address third review changes
    * propulsion board address forth review changes
    * propulsion board address fifth review changes
    * latest progress of the propulsion board layout, but at last I got some issues on routing the 3.3V and GND and may need h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
    [PropulsionBoard.kicad_pcb, PropulsionBoard.kicad_sch, analogSensor.kicad_sch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]
2024-03-19 DAQ CAN Support (#74)
    * initial usb_relay schematics
    * Add screw terminal and part numbers, remove old connector
    * Address all of Dom's comments, except for adding a female USB connector and the electrical rules check
    * change connector to female
    * add footprints
    * Address jack's comments
    * Forgot to save last time
    * resolved comments
    * fixed foorprints
    * added usb footprint
    * began layout
    * added datasheet link to pic
    * added esd protection and termination resistor
    * implemented changes
    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
    [DAQ CAN support.kicad_pcb, DAQ CAN support.kicad_sch]
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
